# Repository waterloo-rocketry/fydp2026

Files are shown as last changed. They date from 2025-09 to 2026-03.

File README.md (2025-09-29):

# FYDP 2026 Electrical & Software

Sisyphus is a regeneratively cooled, 3D-printed liquid rocket engine. There are threee main electrical projects that support this system: Automedon, Achilles, and Theseus

## Automedon
Automedon is a repackaging of the team's existing EGSE stack (namely RLCS, DAQ, and GSPD) within two fully enclosed NEMA panels and with a redesigned power architecture. This vastly improves the robustness and utility of the system
Design doc: https://docs.google.com/document/d/1RASc9nuHLxcU_nNqpzqdATsLbMFS-u7HsDOORrnuTvM/edit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

## Achilles
Achilles, like its namesake, is designed to be an unkillable DAQ module that retains good analog performance. Unlike the team's previous COTS solutions, the system supports up to 30V common mode and differential signals, and is protected up to +/- 60V at the inputs.
DAQ v2 Design Doc (for context): https://docs.google.com/document/d/1antcjPh_7nqCMTjgXxEhXMyPKeuij0gU7g0J603f2qo/edit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

## Theseus
Theseus is the third iteration on the team's integrated propulsion avionics PCB. It is designed to read from pressure transducers, Hall sensors, and RTDs (which are very necessary for regen testing), as well as actuating solenoid valves

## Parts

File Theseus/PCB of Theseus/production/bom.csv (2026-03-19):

Designator | Footprint | Quantity | Value | LCSC Part #
3V3 | TestPoint_Pad_D2.0mm | 1 | TestPoint
C1, C2, C22 | 0603 | 3 | 10u
C10, C11 | 0603 | 2 | 2.2u
C12, C13, C15, C16, C17, C18, C19, C26, C3, C5, C9 | 0603 | 11 | 100n
C14 | 0603 | 1 | 1n
C20 | 0603 | 1 | 0.01uF
C21 | 0603 | 1 | 4.7u
C23, C24, C25, C4 | 0603 | 4 | 0.1u
C6, C7, C8 | 0603 | 3 | 22u
D1 | D_SOD-128 | 1 | PMEG3030EP
D2 | 1206 | 1 | WHITE
D3 | 1206 | 1 | BLUE
D4, D6 | 1206 | 2 | GREEN
D5, D7 | D_SOD-123 | 2 | CDBW140-G
F1 | FUSE_0154005.DR | 1 | 0154005.DRL
FB1 | 0603 | 1 | PE-0603PFB121ST
GND | TestPoint_Keystone_5000-5004_Miniature | 1 | TestPoint
J1 | connector_Harwin_G125-MH104M4-04AD000P | 1 | G125-MH104M4-04AD000P
J2 | 4DB-P108-02 | 1 | 4DB-P108-02
J3 | PinSocket_2x07_P1.27mm_Vertical_SMD | 1 | CN4 STDC14 (Programmer)
J4 | microSD_HC_Molex_47219-2001 | 1 | Micro SD Holder 0472192001
J5, J6, J7, J8 | connector_Harwin_G125–MG10605M4P | 4 | Conn_01x06_Socket
L1 | IND_SPM6530T-2R2M | 1 | SPM6530T-2R2M
Q1, Q2 | SOT_12UW-7_DIO | 2 | DMG1012UW-7
R1 | 0603 | 1 | 33.2k
R10, R11, R7, R8, R9 | 0603 | 5 | 51k
R12, R13, R14 | 0603 | 3 | 150R ±0.1%
R15, R17, R19 | 0603 | 3 | 82K
R16, R18, R20 | 0603 | 3 | 130K
R2 | 0603 | 1 | 10k
R21, R22 | 0603 | 2 | 150k
R23, R24 | 0603 | 2 | 100R
R25, R26 | 0603 | 2 | 649R
R27 | 0603 | 1 | 120R
R3 | 0603 | 1 | 300K
R4 | 0603 | 1 | 100K
R5, R6 | 0603 | 2 | 169R
TC+ | TestPoint_Pad_D2.0mm | 1 | TC1+
U1 | SOT-23-6_Handsoldering | 1 | TPS565201DDC
U2 | SOIC-8_3.9x4.9mm_P1.27mm | 1 | TCAN334
U3 | LQFP-100_14x14mm_P0.5mm | 1 | STM32H750VBTx
U4 | SOIC-8_5.3x5.3mm_P1.27mm | 1 | MX25L25645G
U5 | SOIC-8_3.9x4.9mm_P1.27mm | 1 | MAX6675
Y1 | Oscillator_SMD_Abracon_ASE-4Pin_3.2x2.5mm | 1 | ASE-4.000MHz-L-C-T

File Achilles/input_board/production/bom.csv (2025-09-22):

Designator | Footprint | Quantity | Value | LCSC Part #
C1, C59, C60 | 0805 | 3 | 10uF
C10, C12, C17, C19, C21, C23, C34, C37, C38, C6, C65, C68, C69 | 0805 | 13 | 1uF
C11, C58, C61, C8 | 0805 | 4 | 100nF
C13, C4 | 0805 | 2 | 10nF
C14 | 0805 | 1 | 300pF
C15 | 0805 | 1 | 6.8nF
C16, C18, C20, C22, C24, C25, C26, C27, C28, C29, C30, C31, C32, C33, C36, C70, C71 | 0805 | 17 | 0.1uF
C35 | 0805 | 1 | 0.33uF
C39 | 0805 | 1 | 2.2uF
C40, C43, C44, C45, C46, C47, C48, C49, C50, C51, C52, C53, C54 | 0805 | 13 | 100n
C41 | 0805 | 1 | 1u
C42 | 0805 | 1 | 4.7u
C5, C7 | 0805 | 2 | 4.7uF
C55 | 0805 | 1 | 10u
C56, C57 | 0805 | 2 | 2.2u
C62, C63, C64 | 0805 | 3 | 22uF
C66, C9 | 0805 | 2 | 1.6nF
C67 | 0805 | 1 | C
D1 | 1206 | 1 | BLUE
D2 | 1206 | 1 | GREEN
D3 | 1206 | 1 | RED
D4 | 1206 | 1 | WHITE
D5 | D_SMC_Handsoldering | 1 | SMCJ36CA
D6 | CR_SOD123F_DIO | 1 | B260S1F-7
F1 | 01530009Z | 1 | 5A
IC1 | QFN50P300X300X80-17N-D | 1 | LM5157RTER
IC10 | SOP50P490X110-10N | 1 | ADS8860IDGSR
IC2, IC3, IC4, IC5 | SOP65P640X120-20N | 4 | TMUX7349FPWR
IC6, IC7 | SOP65P640X120-16N | 2 | MUX509IPW
IC8 | SOP65P640X120-28N | 1 | MUX36D08IPW
IC9 | SOP65P640X120-16N | 1 | MUX508IPW
J1 | TerminalBlock_Phoenix_MKDS-1,5-2-5.08_1x02_P5.08mm_Horizontal | 1 | Screw_Terminal_01x02
J10 | PinSocket_2x02_P1.27mm_Vertical_SMD | 1 | Programmer
J11, J7 | TerminalBlock_Phoenix_MPT-0,5-2-2.54_1x02_P2.54mm_Horizontal | 2 | Screw_Terminal_01x02
J2 | PinHeader_1x03_P2.54mm_Vertical | 1 | Screw_Terminal_01x03
J3, J4, J5, J6 | TerminalBlock_Phoenix_MPT-0,5-8-2.54_1x08_P2.54mm_Horizontal | 4 | Screw_Terminal_01x08
J8 | CUI_UJ2-BH-1-TH | 1 | USB_B
J9 | PinHeader_1x03_P2.54mm_Vertical | 1 | CAN
L1 | IND_BOURNS_SRR5018 | 1 | SRR5018-3R9Y
L2 | IND_SRP1265A-2R2M | 1 | SRP1265A-2R2M
Q1 | VSON-8_3.3x3.3mm_P0.65mm_NexFET | 1 | CSD19537Q3
Q2 | SOT-23 | 1 | BSS138
R1 | 0805 | 1 | 510R
R10 | 0805 | 1 | 17kR
R11 | 0805 | 1 | 34kR
R12, R17, R18, R43, R47 | 0805 | 5 | 10kR
R13, R41 | 0805 | 2 | 20mR
R14 | 0805 | 1 | 203kR
R15 | 0805 | 1 | 1.29kR
R16 | 0805 | 1 | 75kR
R19, R4, R44 | 0805 | 3 | 500R
R2 | 0805 | 1 | 1.3kR
R20 | 0805 | 1 | 2.43kR
R21 | 0805 | 1 | 1.33k
R22 | 0805 | 1 | 9.76kR
R23, R24, R25, R26, R27, R28, R29, R30 | 0805 | 8 | 1kR
R3 | 0805 | 1 | 150R
R32 | 0805 | 1 | 6kR
R33 | 0805 | 1 | 1.2kR
R34 | 0805 | 1 | 667R
R35 | 0805 | 1 | 122R
R36 | 0805 | 1 | 60.6R
R37 | 0805 | 1 | 12R
R38 | 0805 | 1 | 6R
R39 | 0805 | 1 | 51kR
R40 | 0805 | 1 | 24kR
R42 | 0805 | 1 | 17.4kR
R45, R46 | 0805 | 2 | R_US
R5 | 0805 | 1 | 435kR
R6 | 0805 | 1 | 56kR
R7 | 0805 | 1 | 9.09kR
R8 | 0805 | 1 | 38.3kR
R9 | 0805 | 1 | 374kR
RN1, RN2 | SOT-23 | 2 | MAX5490TA05000-T
U1 | HTSSOP-20-1EP_4.4x6.5mm_P0.65mm_EP3.4x6.5mm_Mask2.96x2.96mm_ThermalVias | 1 | TPS26631PWP
U10, U11, U4, U5, U6, U7, U8, U9 | VSSOP-8_3x3mm_P0.65mm | 8 | INA849DGK
U12 | VSSOP-8_3x3mm_P0.65mm | 1 | REF6050xDGK
U13 | TO-263-3_TabPin2 | 1 | uA7805
U14 | SOT-23-5 | 1 | TPS76933
U15 | SOIC-8_3.9x4.9mm_P1.27mm | 1 | MCP2562
U16 | LQFP-144_20x20mm_P0.5mm | 1 | STM32H750ZBTx
U17 | SOT-23-6 | 1 | TPS565201
U18 | SOT-23-5_HandSoldering | 1 | INA180A3
U2 | Texas_RGW0020A_VQFN-20-1EP_5x5mm_P0.65mm_EP3.15x3.15mm_ThermalVias | 1 | TPS7A4701xRGW
U3 | SC70-5_DCK_TEX | 1 | INA290A3

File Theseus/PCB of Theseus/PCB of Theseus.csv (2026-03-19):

Reference | Qty | Value | DNP | Exclude from BOM | Exclude from Board | Footprint | Datasheet
C1,C2,C22 | 3 | 10u |  |  |  | Capacitor_SMD:C_0603_1608Metric_Pad1.08x0.95mm_HandSolder | ~
C3,C5,C9,C12,C13,C15,C16,C17,C18,C19,C26 | 11 | 100n |  |  |  | Capacitor_SMD:C_0603_1608Metric_Pad1.08x0.95mm_HandSolder | ~
C4,C23,C24,C25 | 4 | 0.1u |  |  |  | Capacitor_SMD:C_0603_1608Metric_Pad1.08x0.95mm_HandSolder | ~
C6,C7,C8 | 3 | 22u |  |  |  | Capacitor_SMD:C_0603_1608Metric_Pad1.08x0.95mm_HandSolder | ~
C10,C11 | 2 | 2.2u |  |  |  | Capacitor_SMD:C_0603_1608Metric_Pad1.08x0.95mm_HandSolder | ~
C14 | 1 | 1n |  |  |  | Capacitor_SMD:C_0603_1608Metric_Pad1.08x0.95mm_HandSolder | ~
C20 | 1 | 0.01uF |  |  |  | Capacitor_SMD:C_0603_1608Metric_Pad1.08x0.95mm_HandSolder | ~
C21 | 1 | 4.7u |  |  |  | Capacitor_SMD:C_0603_1608Metric_Pad1.08x0.95mm_HandSolder | ~
D1 | 1 | PMEG3030EP |  |  |  | Diode_SMD:D_SOD-128 | https://assets.nexperia.com/documents/data-sheet/PMEG3030EP.pdf
D2 | 1 | WHITE |  |  |  | LED_SMD:LED_1206_3216Metric_Pad1.42x1.75mm_HandSolder | ~
D3 | 1 | BLUE |  |  |  | LED_SMD:LED_1206_3216Metric_Pad1.42x1.75mm_HandSolder | ~
D4,D6 | 2 | GREEN |  |  |  | LED_SMD:LED_1206_3216Metric_Pad1.42x1.75mm_HandSolder | ~
D5,D7 | 2 | CDBW140-G |  |  |  | Diode_SMD:D_SOD-123 | https://www.mouser.ca/datasheet/3/819/1/CDBW120-G%20Thru.%20CDBW140-G%20RevE.pdf
F1 | 1 | 0154005.DRL |  |  |  | Fydp_footprints:FUSE_0154005.DR | ~
FB1 | 1 | PE-0603PFB121ST |  |  |  | Resistor_SMD:R_0603_1608Metric_Pad0.98x0.95mm_HandSolder | ~
H1,H2,H3,H4 | 4 | MountingHole |  | Excluded from BOM |  | MountingHole:MountingHole_3.2mm_M3_ISO14580 | ~
J1 | 1 | G125-MH104M4-04AD000P |  |  |  | canhw_footprints:connector_Harwin_G125-MH104M4-04AD000P | https://content.harwin.com/m/91a65d72bc24bdea/original/DRG-03150-Technical-Drawing-Datasheet-G125-MH1XXM4-XXAD000P-pdf.pdf
J2 | 1 | 4DB-P108-02 |  |  |  | canhw_footprints:4DB-P108-02 | ~
J3 | 1 | CN4 STDC14 (Programmer) |  |  |  | Connector_PinSocket_1.27mm:PinSocket_2x07_P1.27mm_Vertical_SMD | ~
J4 | 1 | Micro SD Holder 0472192001 |  |  |  | Connector_Card:microSD_HC_Molex_47219-2001 | https://www.we-online.com/components/products/datasheet/693072010801.pdf
J5,J6,J7,J8 | 4 | Conn_01x06_Socket |  |  |  | canhw_footprints:connector_Harwin_G125–MG10605M4P | ~
L1 | 1 | SPM6530T-2R2M |  |  |  | Fydp_footprints:IND_SPM6530T-2R2M | ~
Q1,Q2 | 2 | DMG1012UW-7 |  |  |  | Fydp_footprints:SOT_12UW-7_DIO | ~
R1 | 1 | 33.2k |  |  |  | Resistor_SMD:R_0603_1608Metric_Pad0.98x0.95mm_HandSolder | ~
R2 | 1 | 10k |  |  |  | Resistor_SMD:R_0603_1608Metric_Pad0.98x0.95mm_HandSolder | ~
R3 | 1 | 300K |  |  |  | Resistor_SMD:R_0603_1608Metric_Pad0.98x0.95mm_HandSolder | ~
R4 | 1 | 100K |  |  |  | Resistor_SMD:R_0603_1608Metric_Pad0.98x0.95mm_HandSolder | ~
R5,R6 | 2 | 169R |  |  |  | Resistor_SMD:R_0603_1608Metric_Pad0.98x0.95mm_HandSolder | ~
R7,R8,R9,R10,R11 | 5 | 51k |  |  |  | Resistor_SMD:R_0603_1608Metric_Pad0.98x0.95mm_HandSolder | ~
R12,R13,R14 | 3 | 150R ±0.1% |  |  |  | Resistor_SMD:R_0603_1608Metric_Pad0.98x0.95mm_HandSolder | ~
R15,R17,R19 | 3 | 82K |  |  |  | Resistor_SMD:R_0603_1608Metric_Pad0.98x0.95mm_HandSolder | ~
R16,R18,R20 | 3 | 130K |  |  |  | Resistor_SMD:R_0603_1608Metric_Pad0.98x0.95mm_HandSolder | ~
R21,R22 | 2 | 150k |  |  |  | Resistor_SMD:R_0603_1608Metric_Pad0.98x0.95mm_HandSolder | ~
R23,R24 | 2 | 100R |  |  |  | Resistor_SMD:R_0603_1608Metric_Pad0.98x0.95mm_HandSolder | ~
R25,R26 | 2 | 649R |  |  |  | Resistor_SMD:R_0603_1608Metric_Pad0.98x0.95mm_HandSolder | ~
R27 | 1 | 120R | DNP |  |  | Resistor_SMD:R_0603_1608Metric_Pad0.98x0.95mm_HandSolder | ~
TP1 | 1 | TestPoint |  |  |  | TestPoint:TestPoint_Pad_D2.0mm | ~
TP2 | 1 | TestPoint |  |  |  | TestPoint:TestPoint_Keystone_5000-5004_Miniature | ~
TP3 | 1 | TC1+ |  |  |  | TestPoint:TestPoint_Pad_D2.0mm | ~
U1 | 1 | TPS565201DDC |  |  |  | Package_TO_SOT_SMD:SOT-23-6_Handsoldering | https://www.ti.com/lit/ds/symlink/tps565201.pdf
U2 | 1 | TCAN334 |  |  |  | Package_SO:SOIC-8_3.9x4.9mm_P1.27mm | http://www.ti.com/lit/ds/symlink/tcan337.pdf
U3 | 1 | STM32H750VBTx |  |  |  | Package_QFP:LQFP-100_14x14mm_P0.5mm | https://www.st.com/resource/en/datasheet/stm32h750vb.pdf
U4 | 1 | MX25L25645G |  |  |  | Package_SO:SOIC-8_5.3x5.3mm_P1.27mm | https://www.mxic.com.tw/Lists/Datasheet/Attachments/8906/MX25L25645G,%203V,%20256Mb,%20v2.0.pdf
U5 | 1 | MAX6675 |  |  |  | Package_SO:SOIC-8_3.9x4.9mm_P1.27mm | https://www.analog.com/media/en/technical-documentation/data-sheets/MAX6675.pdf
Y1 | 1 | ASE-4.000MHz-L-C-T |  |  |  | Oscillator:Oscillator_SMD_Abracon_ASE-4Pin_3.2x2.5mm | http://www.abracon.com/Oscillators/ASV.pdf

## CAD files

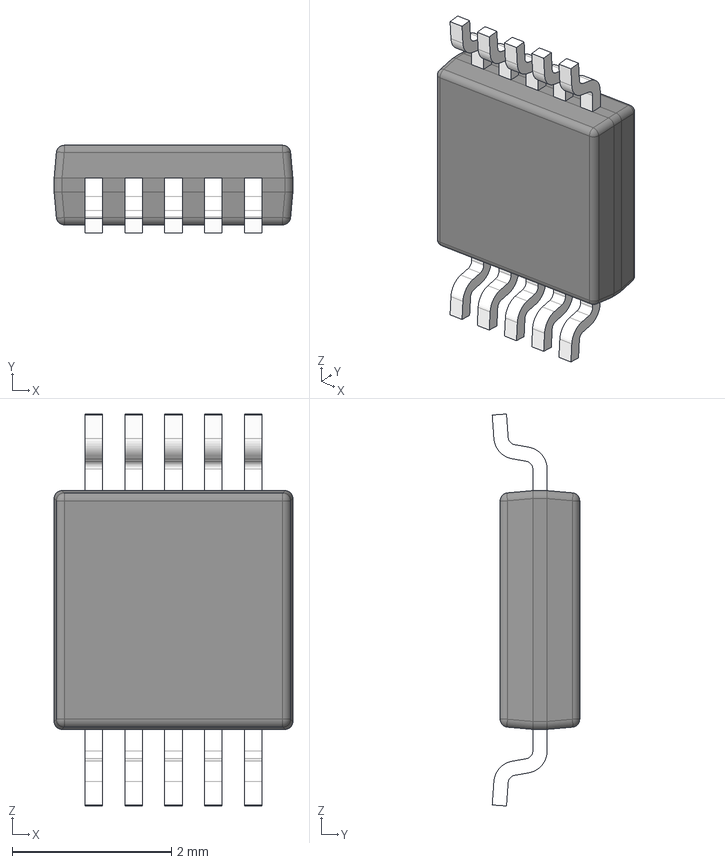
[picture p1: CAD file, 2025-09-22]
Achilles/input_board/3D/ADS8860IDGSR.stp
3.00 x 1.10 x 4.93 mm
BODY-SO
LEAD-SO x 10
PIN1-ID

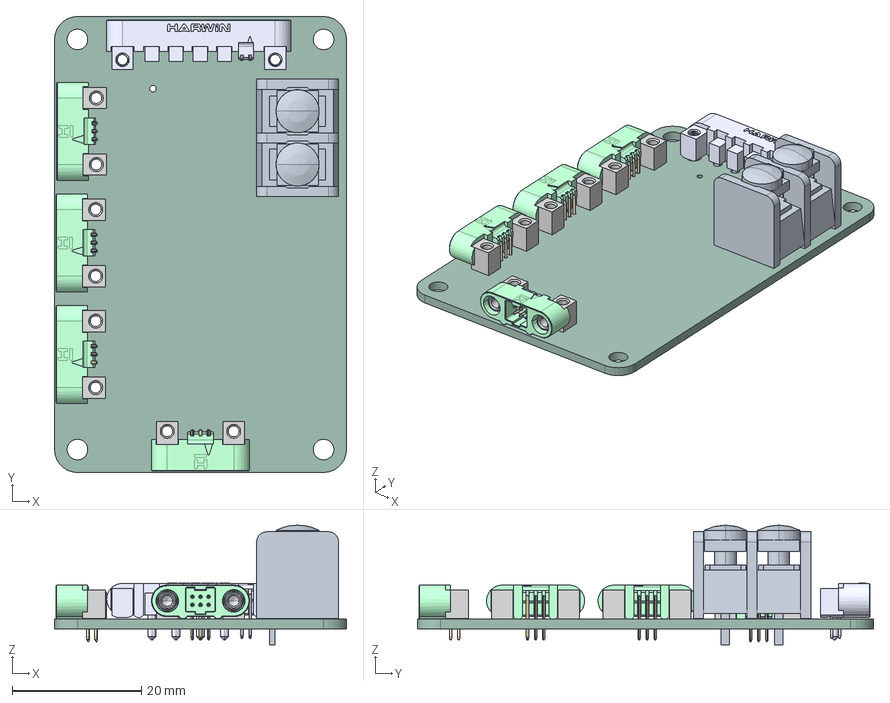
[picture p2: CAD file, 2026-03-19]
Theseus/PCB of Theseus/PCB of Theseus.step
45.2 x 70.6 x 18.5 mm
4DB-P108-02
G125-3270696 x 4
G125-1060005_BENT x 12
G125-1070005_BENT x 12
g125-mh104m4-04ad000p
PCB of Theseus_PCB

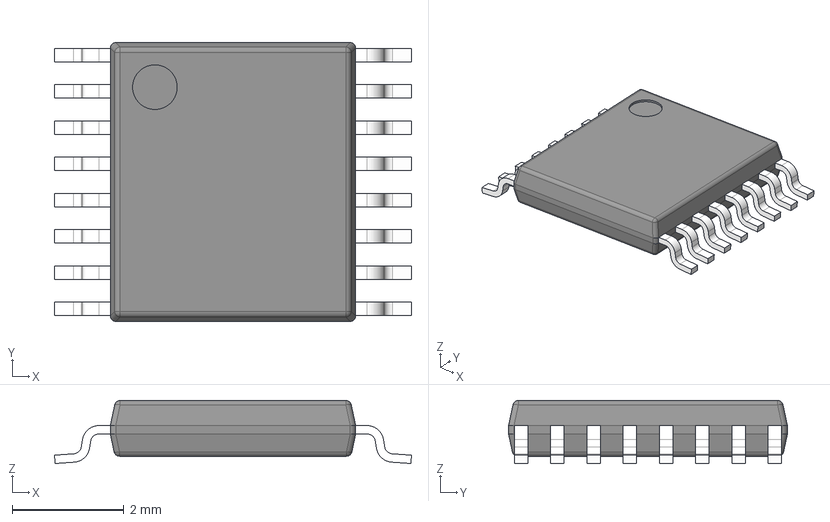
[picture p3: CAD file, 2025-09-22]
Achilles/input_board/3D/MUX509IPW.stp
6.40 x 5.00 x 1.13 mm
BODY-TSSOP
LEAD-TSSOP x 16
PIN1

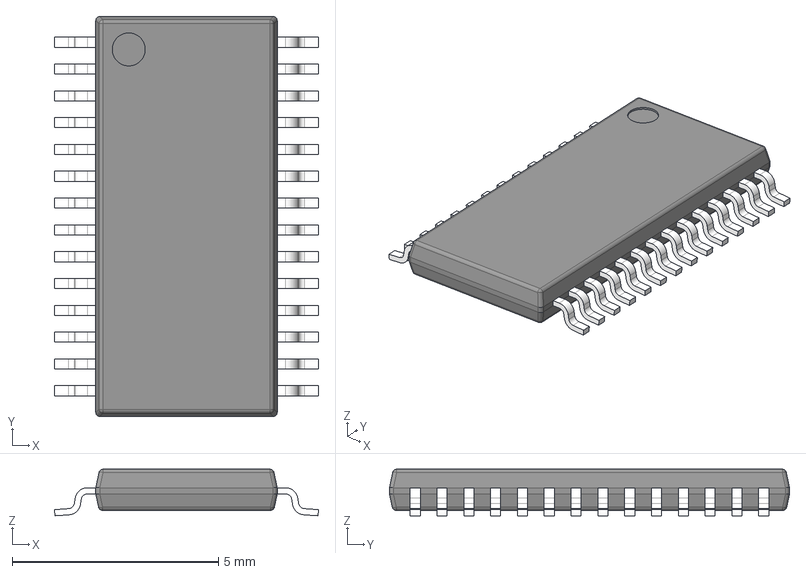
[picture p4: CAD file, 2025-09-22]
Achilles/input_board/3D/MUX36D08IPW.stp
6.40 x 9.70 x 1.13 mm
BODY-TSSOP
LEAD-TSSOP x 28
PIN1

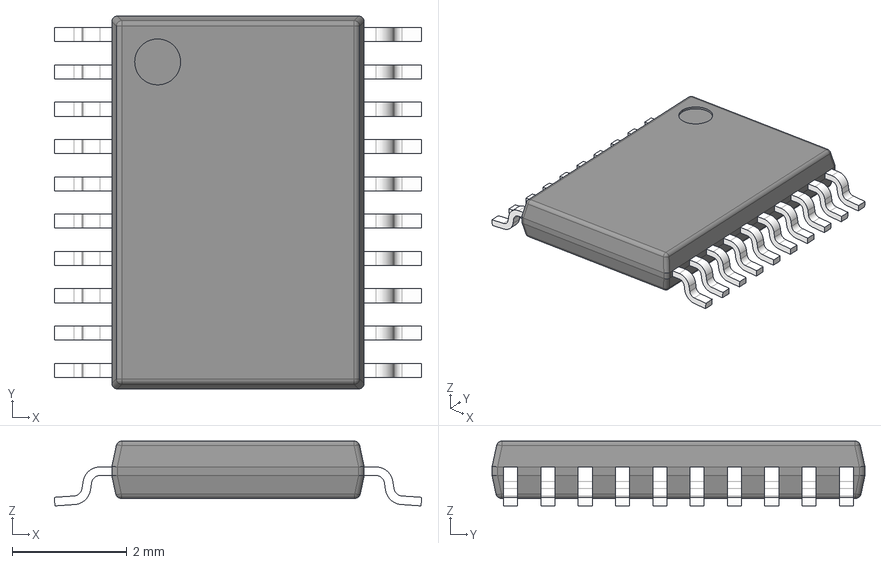
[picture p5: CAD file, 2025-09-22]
Achilles/input_board/3D/TMUX7348FPWR.stp
6.40 x 6.50 x 1.13 mm
BODY-TSSOP
LEAD-TSSOP x 20
PIN1

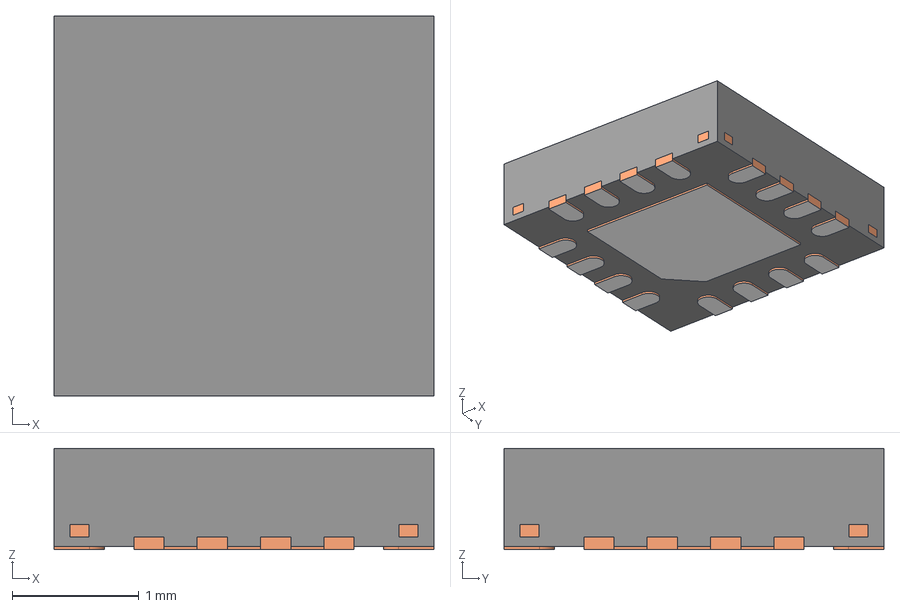
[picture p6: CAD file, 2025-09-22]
Achilles/input_board/3D/LM5157RTER.stp
3.00 x 3.00 x 0.8 mm
BODY-QFN
FRAME-RTE0016C
PIN1-ID

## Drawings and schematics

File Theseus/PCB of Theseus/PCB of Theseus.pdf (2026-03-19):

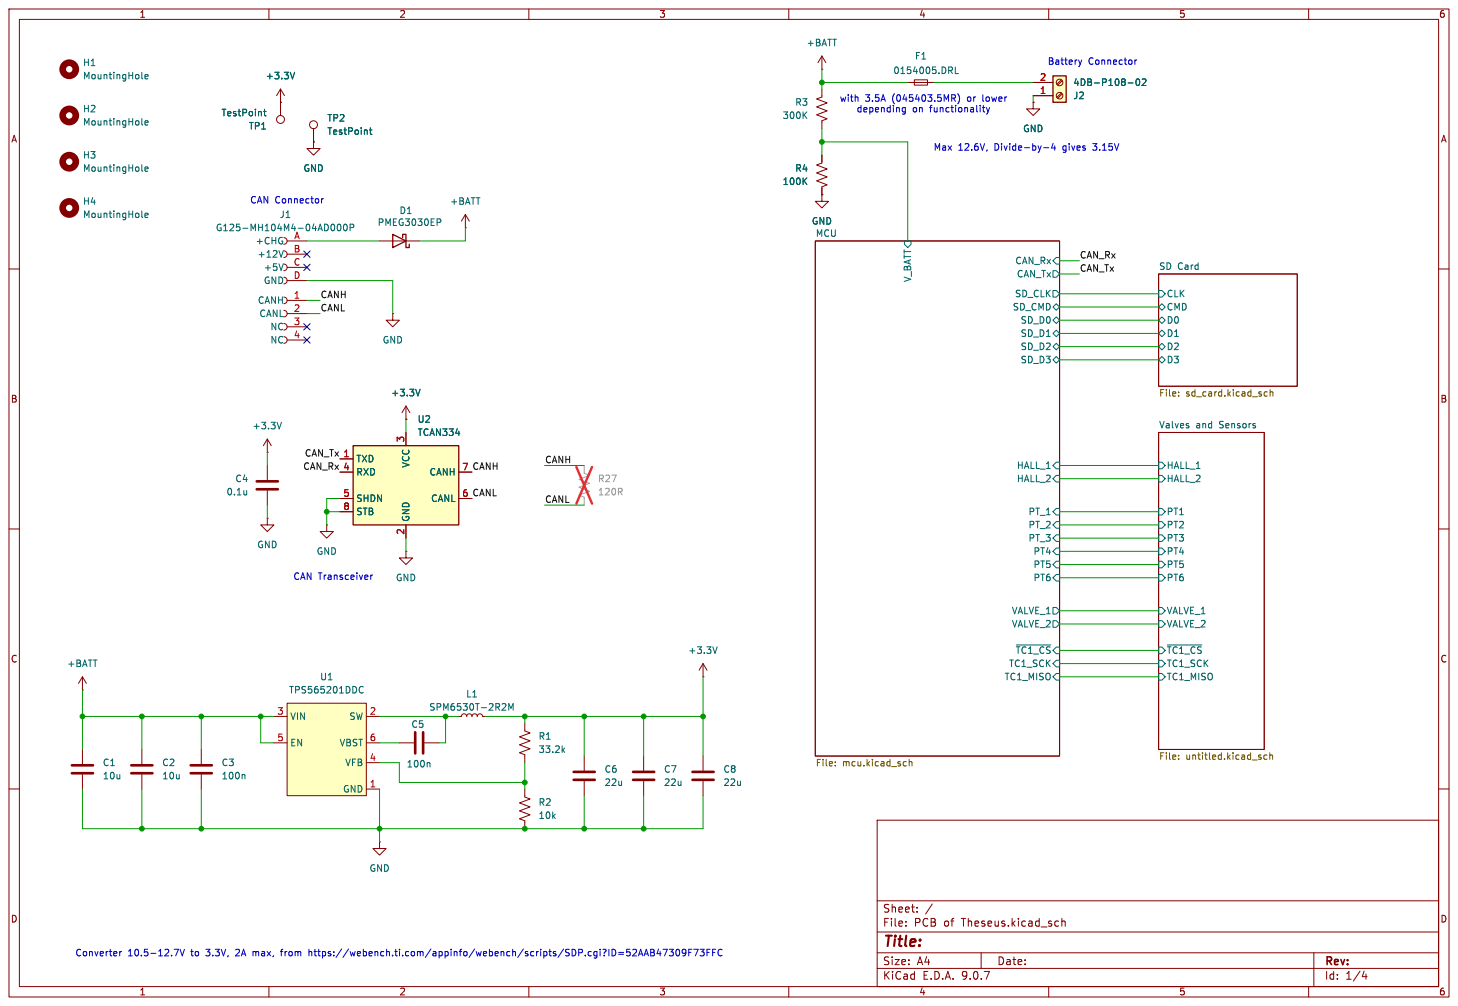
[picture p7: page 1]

CANH 1 CANL 2 NC 3 NC 4

CLK CMD
VALVE_2 Valves and Sensors File: untitled.kicad_sch

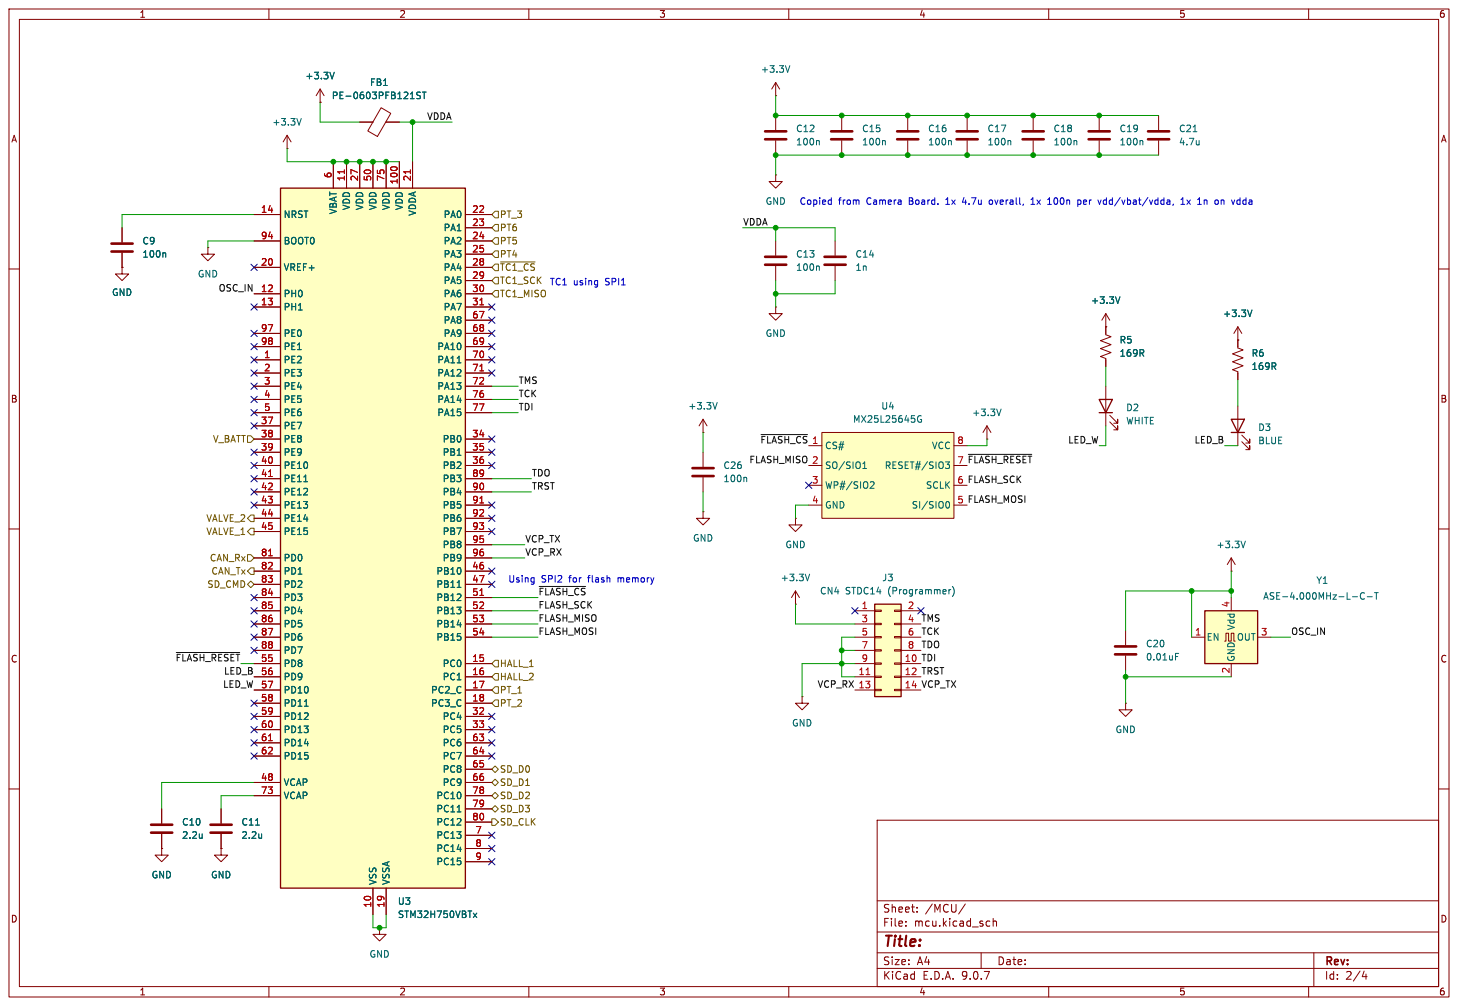
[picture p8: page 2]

6 VDD 11 VDD 27 VDD 50 VSS 10 VDD 75 VSSA 19 VDD 100 VDDA 21 PA0 22 PA1 23 PA2 24 PA3 25 PA4 28 PA5 29 PA6 30 PA7 31 PA8 67 PA9 68 PA10 69 PA11 70 PA12 71 PA13 72 PA14 76 PA15 77 PB0 34 PB1 35 PB2 36 PB3 89 PB4 90 PB5 91 PB6 92 PB7 93 PB8 95 PB9 96 PB10 46 PB11 47 PB12 51 PB13 52 PB14 53 PB15 54 PC0 15 PC1 16 PC2_C 17 PC3_C 18 PC4 32 PC5 33 PC6 63 PC7 64 PC8 65 PC9 66 PC10 78 PC11 79 PC12 80 PC13 7 PC14 8 PC15 9 C10

6 VDD 11 VDD 27 VDD 50 VSS 10 VDD 75 VSSA 19 VDD 100 VDDA 21 PA0 22 PA1 23 PA2 24 PA3 25 PA4 28 PA5 29 PA6 30 PA7 31 PA8 67 PA9 68 PA10 69 PA11 70 PA12 71 PA13 72 PA14 76 PA15 77 PB0 34 PB1 35 PB2 36 PB3 89 PB4 90 PB5 91 PB6 92 PB7 93 PB8 95 PB9 96 PB10 46 PB11 47 PB12 51 PB13 52 PB14 53 PB15 54 PC0 15 PC1 16 PC2_C 17 PC3_C 18 PC4 32 PC5 33 PC6 63 PC7 64 PC8 65 PC9 66 PC10 78 PC11 79 PC12 80 PC13 7 PC14 8 PC15 9 U3STM32H750VBTx

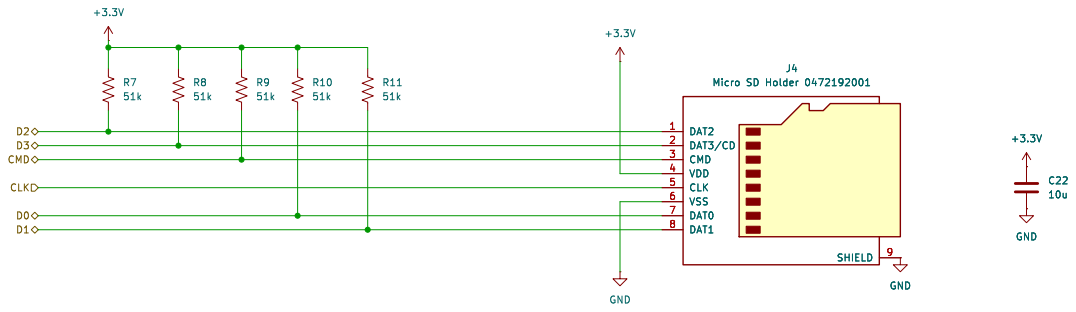
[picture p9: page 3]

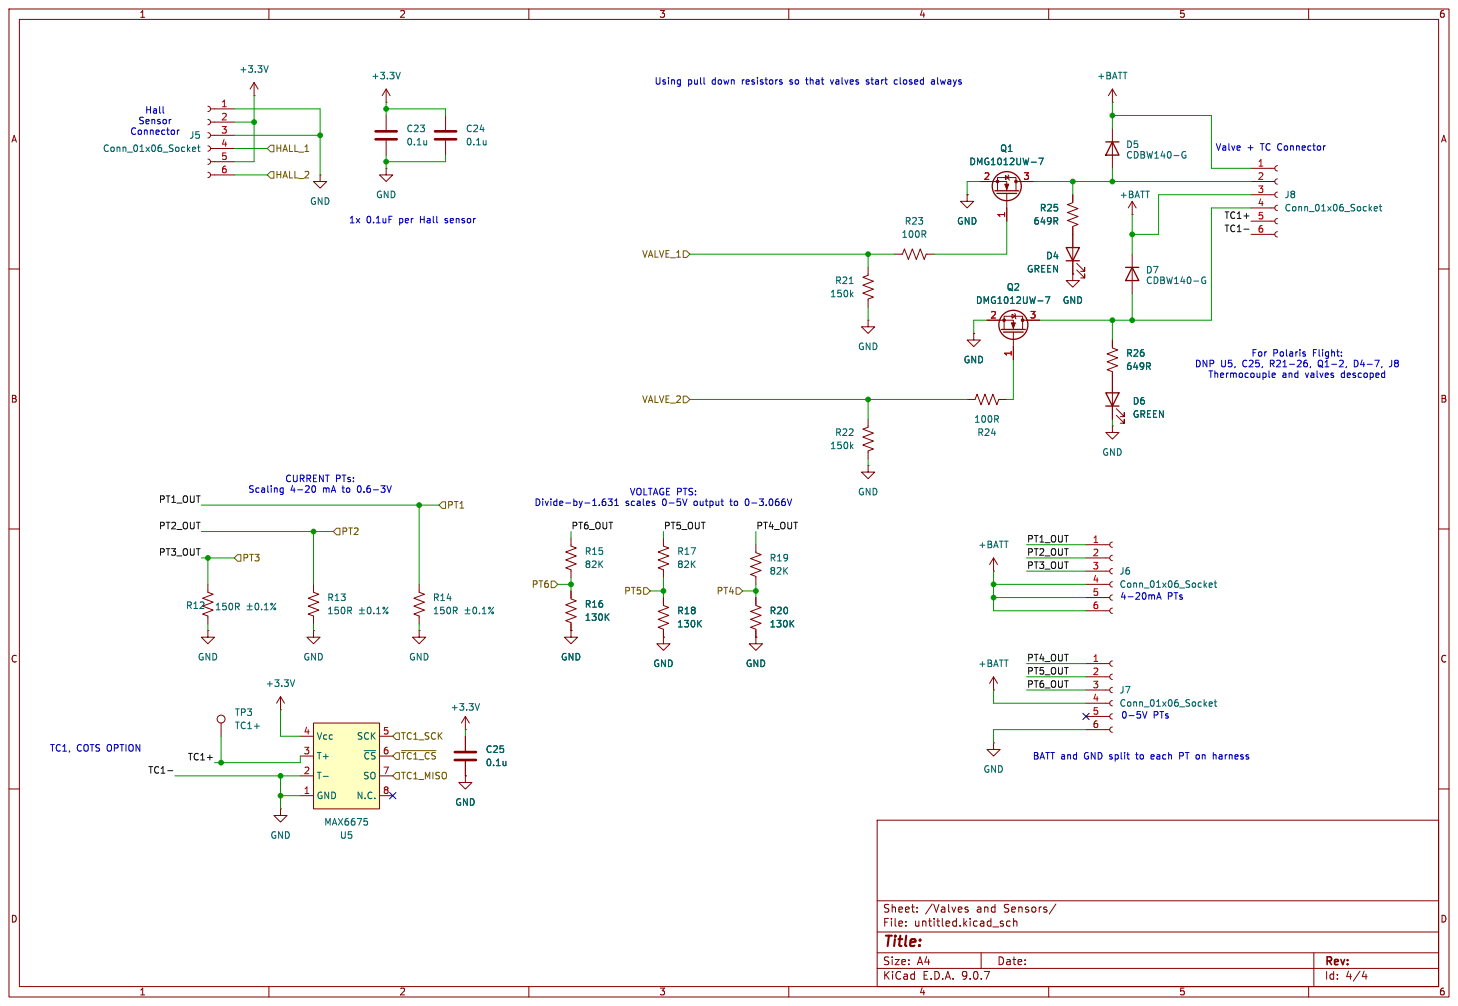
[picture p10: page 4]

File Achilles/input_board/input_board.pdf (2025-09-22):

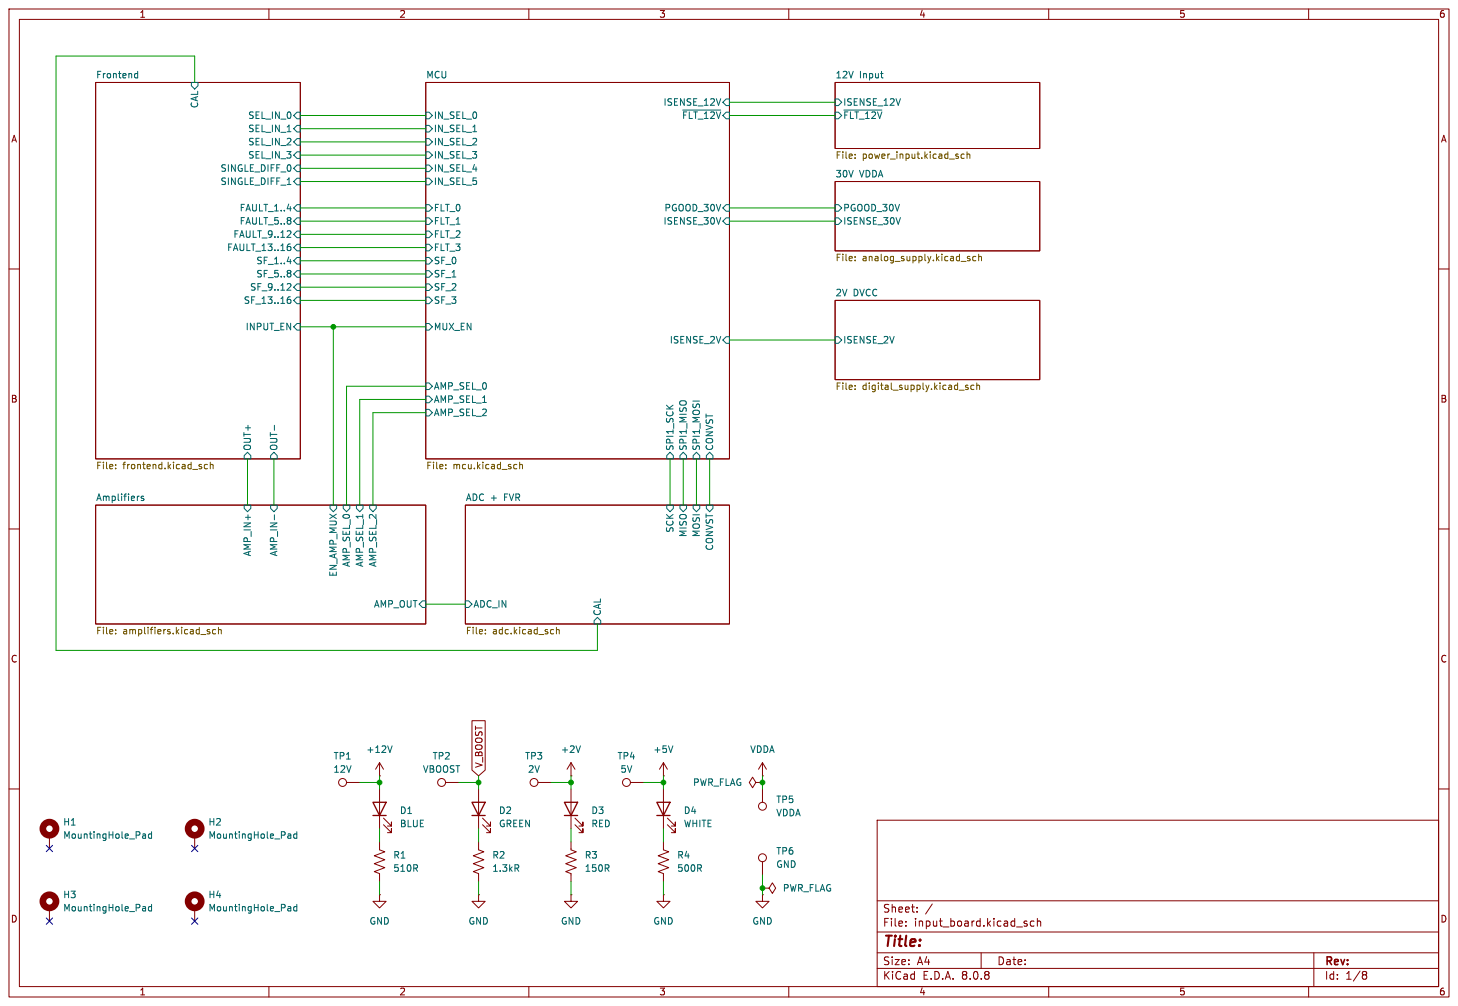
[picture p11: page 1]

Id: 1/8 Title: File: input_board.kicad_sch Sheet: /

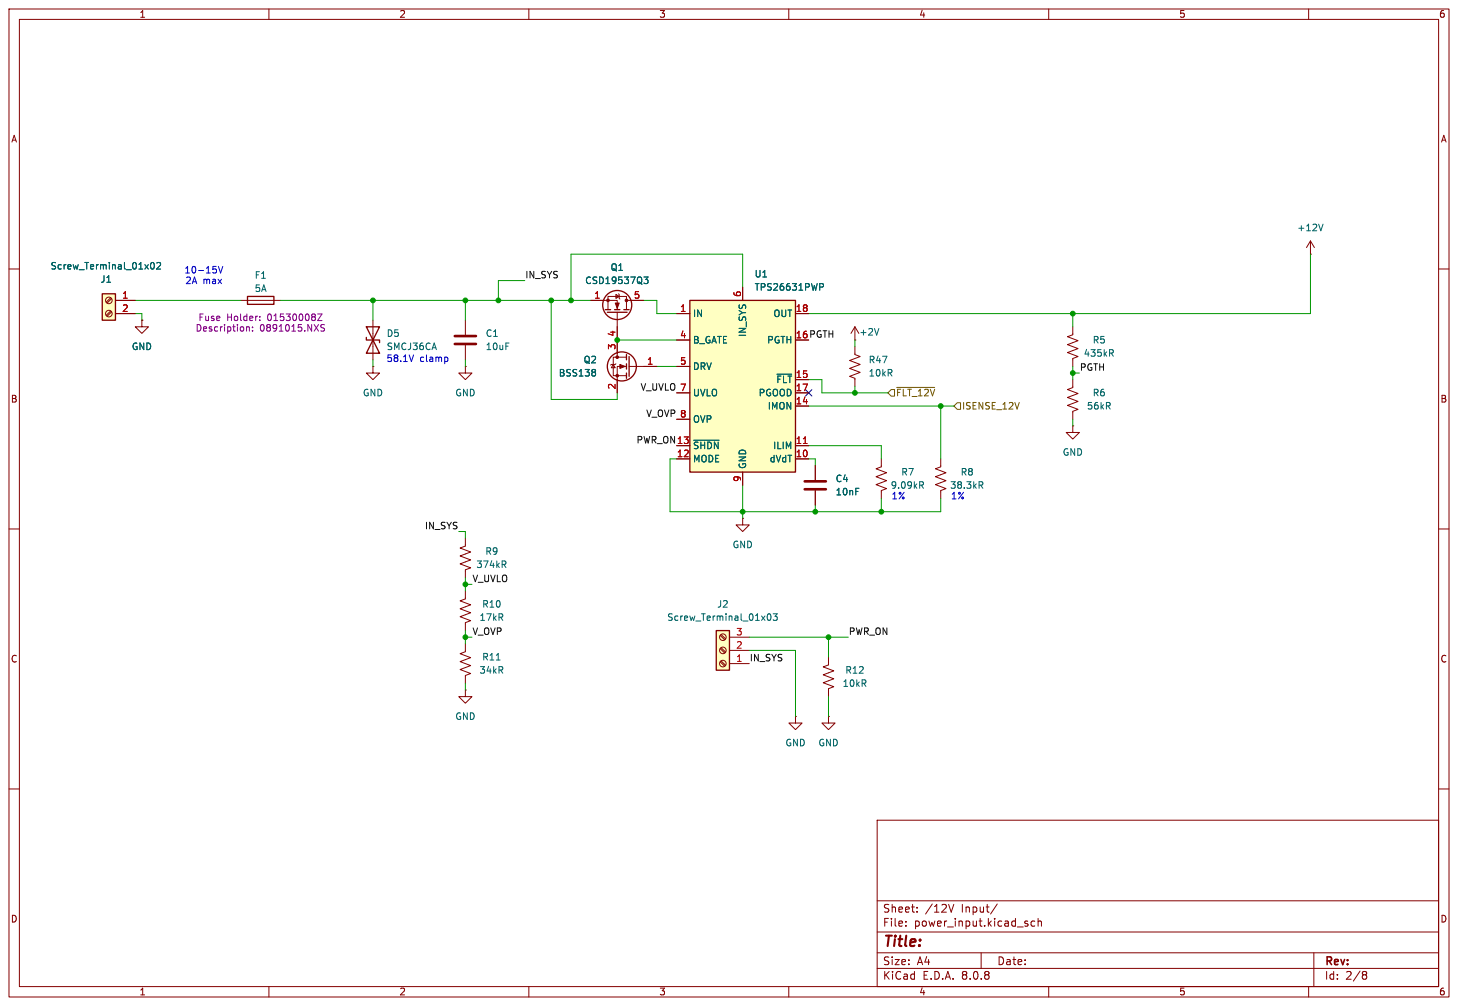
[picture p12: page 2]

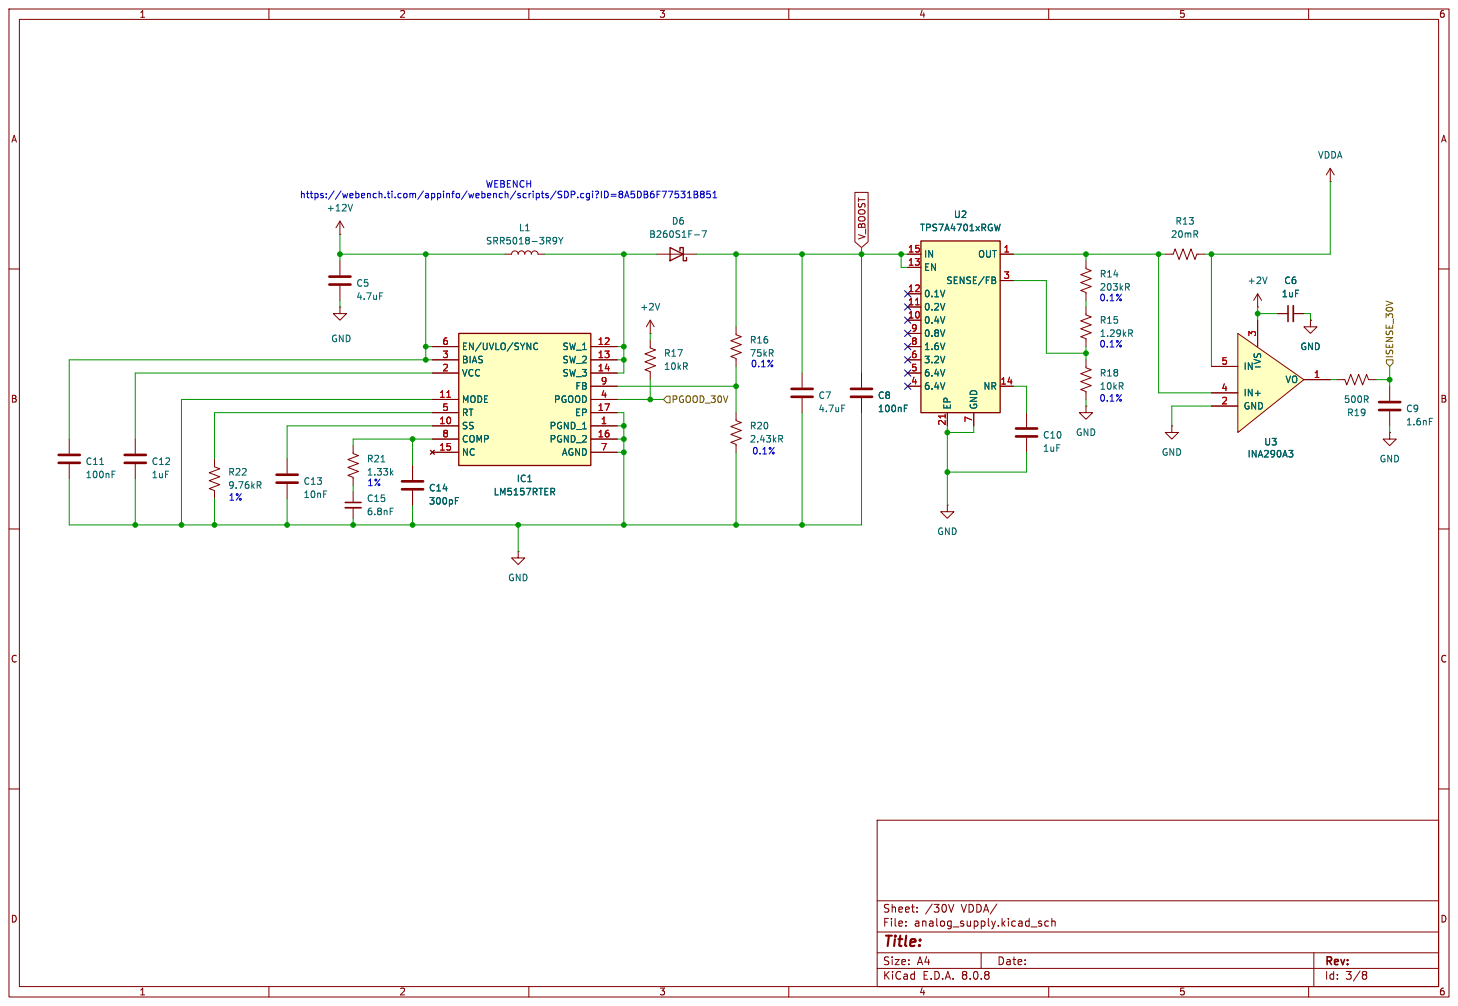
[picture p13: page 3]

https://webench.ti.com/appinfo/webench/scripts/SDP.cgi?ID=8A5DB6F77531B851

Id: 3/8 Title: File: analog_supply.kicad_sch Sheet: /30V VDDA/

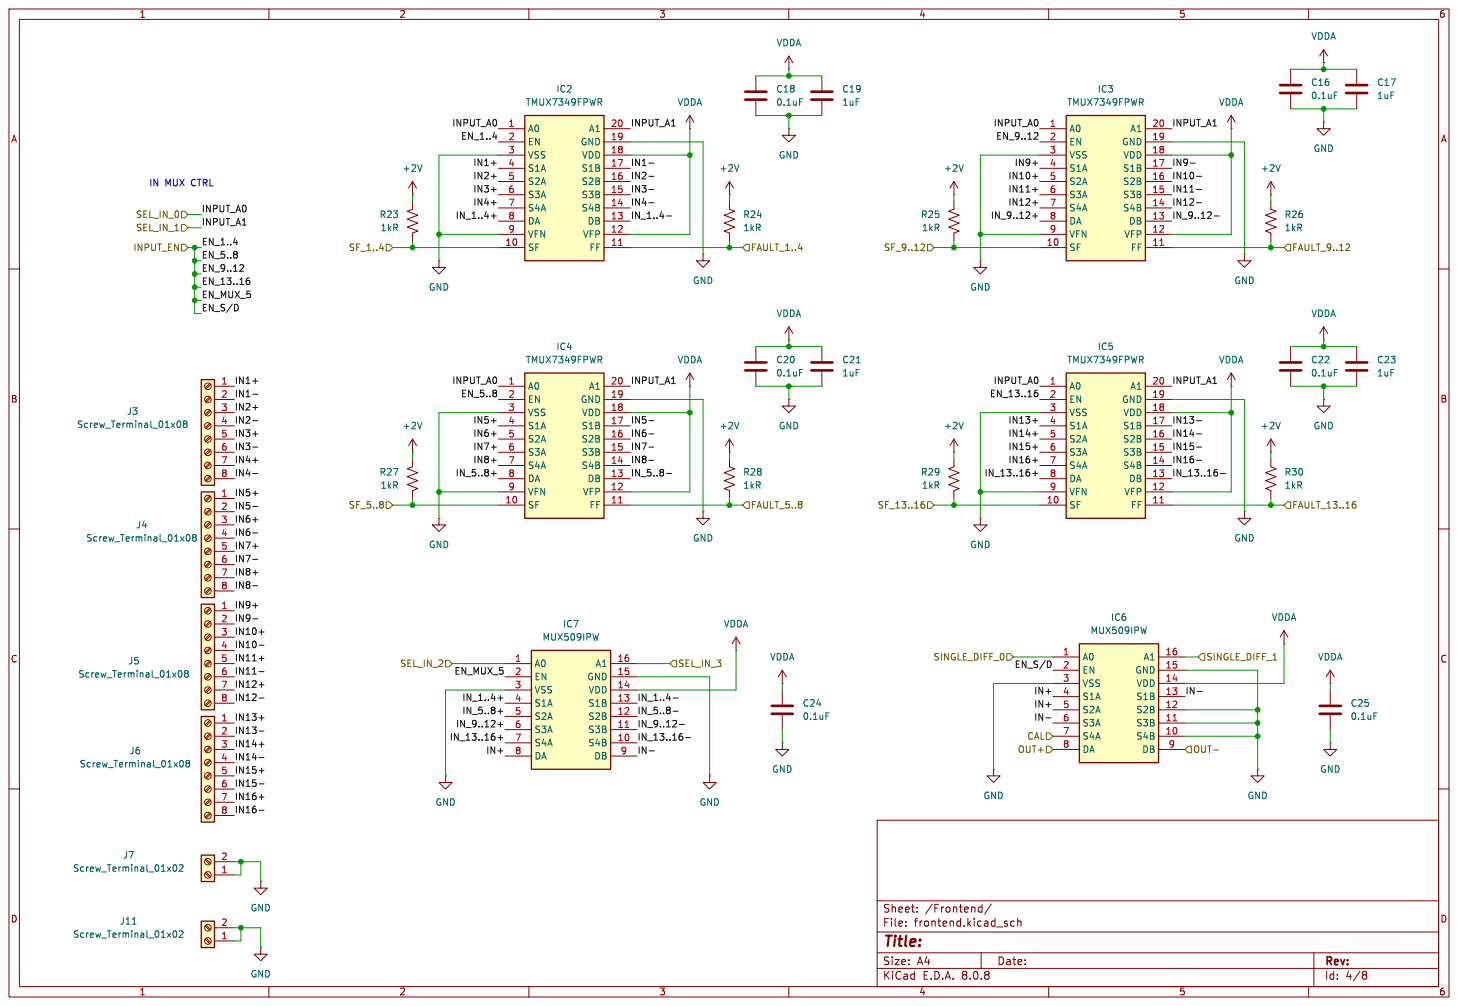
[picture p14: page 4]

Id: 4/8 Title: File: frontend.kicad_sch Sheet: /Frontend/ R29

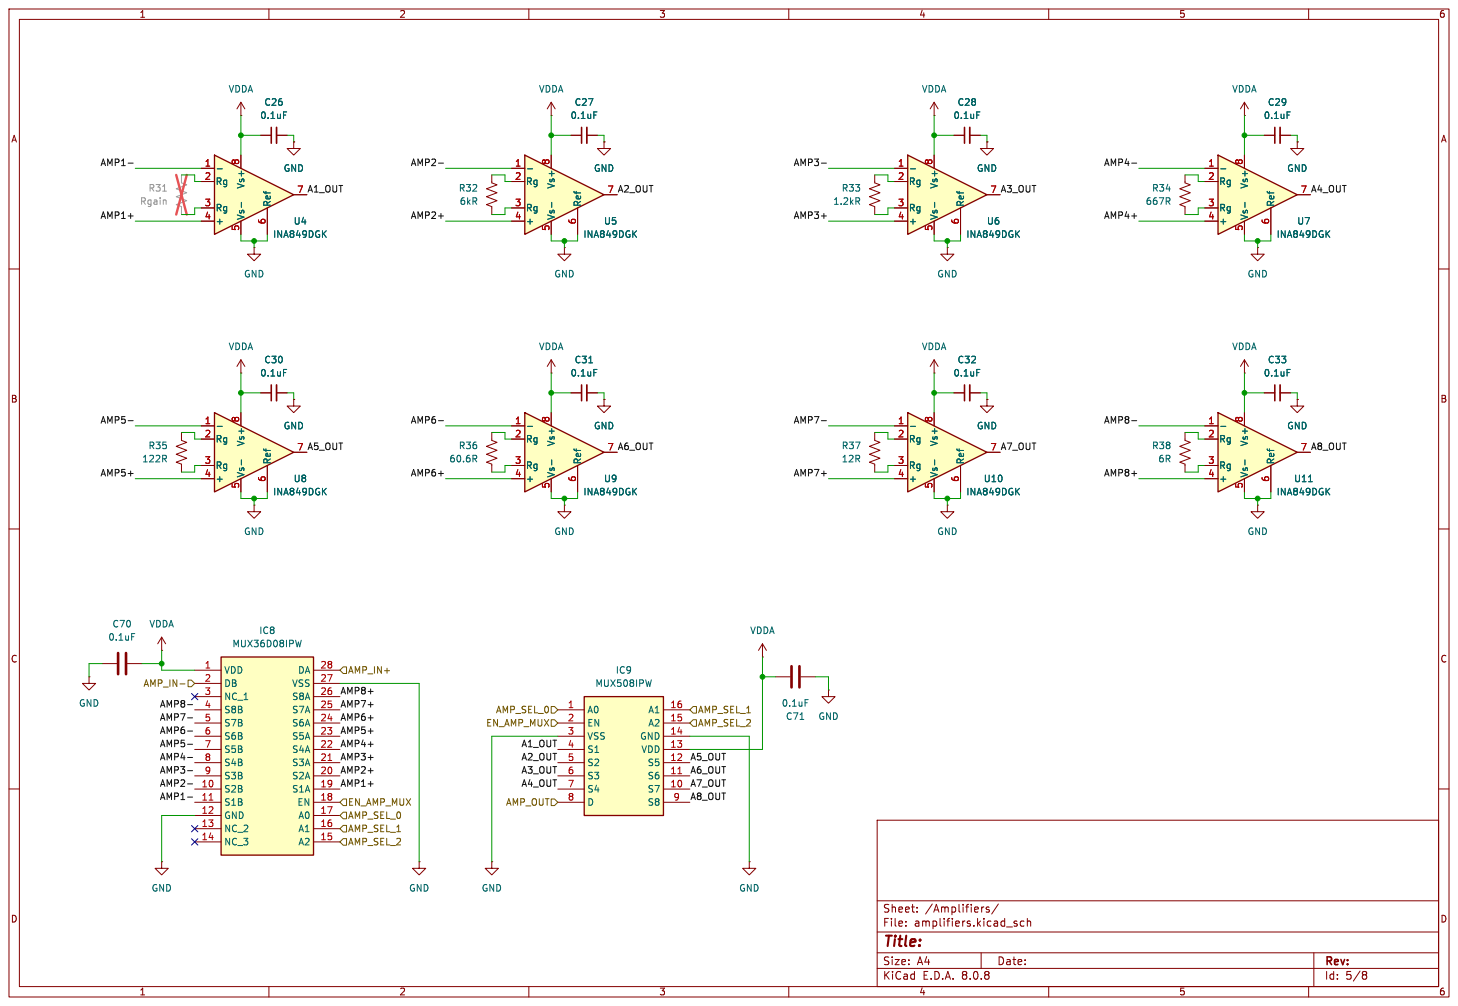
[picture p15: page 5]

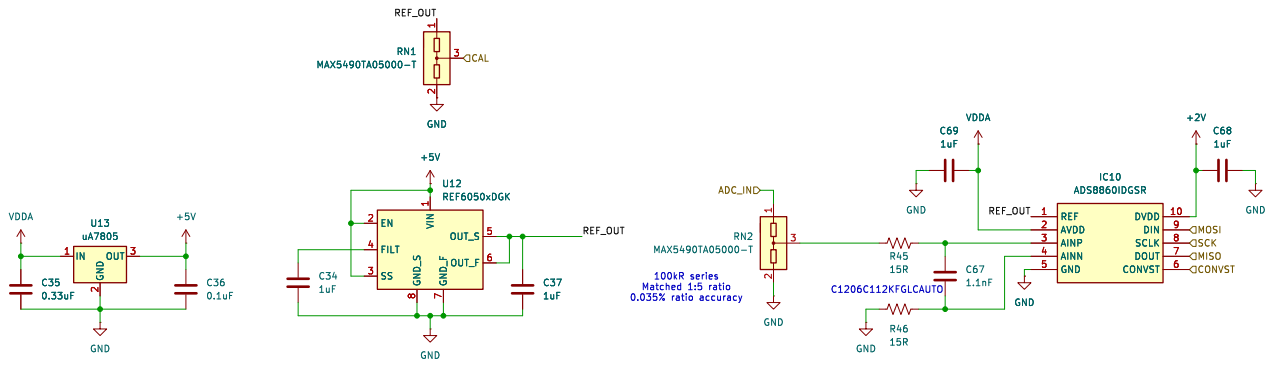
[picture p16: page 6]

1 2 RN1 3 MAX5490TA05000-T REF 1 DVDD 10 AVDD 2 AINP 3 AINN 4 GND 5 CONVST 6 DOUT 7 SCLK 8 DIN 9

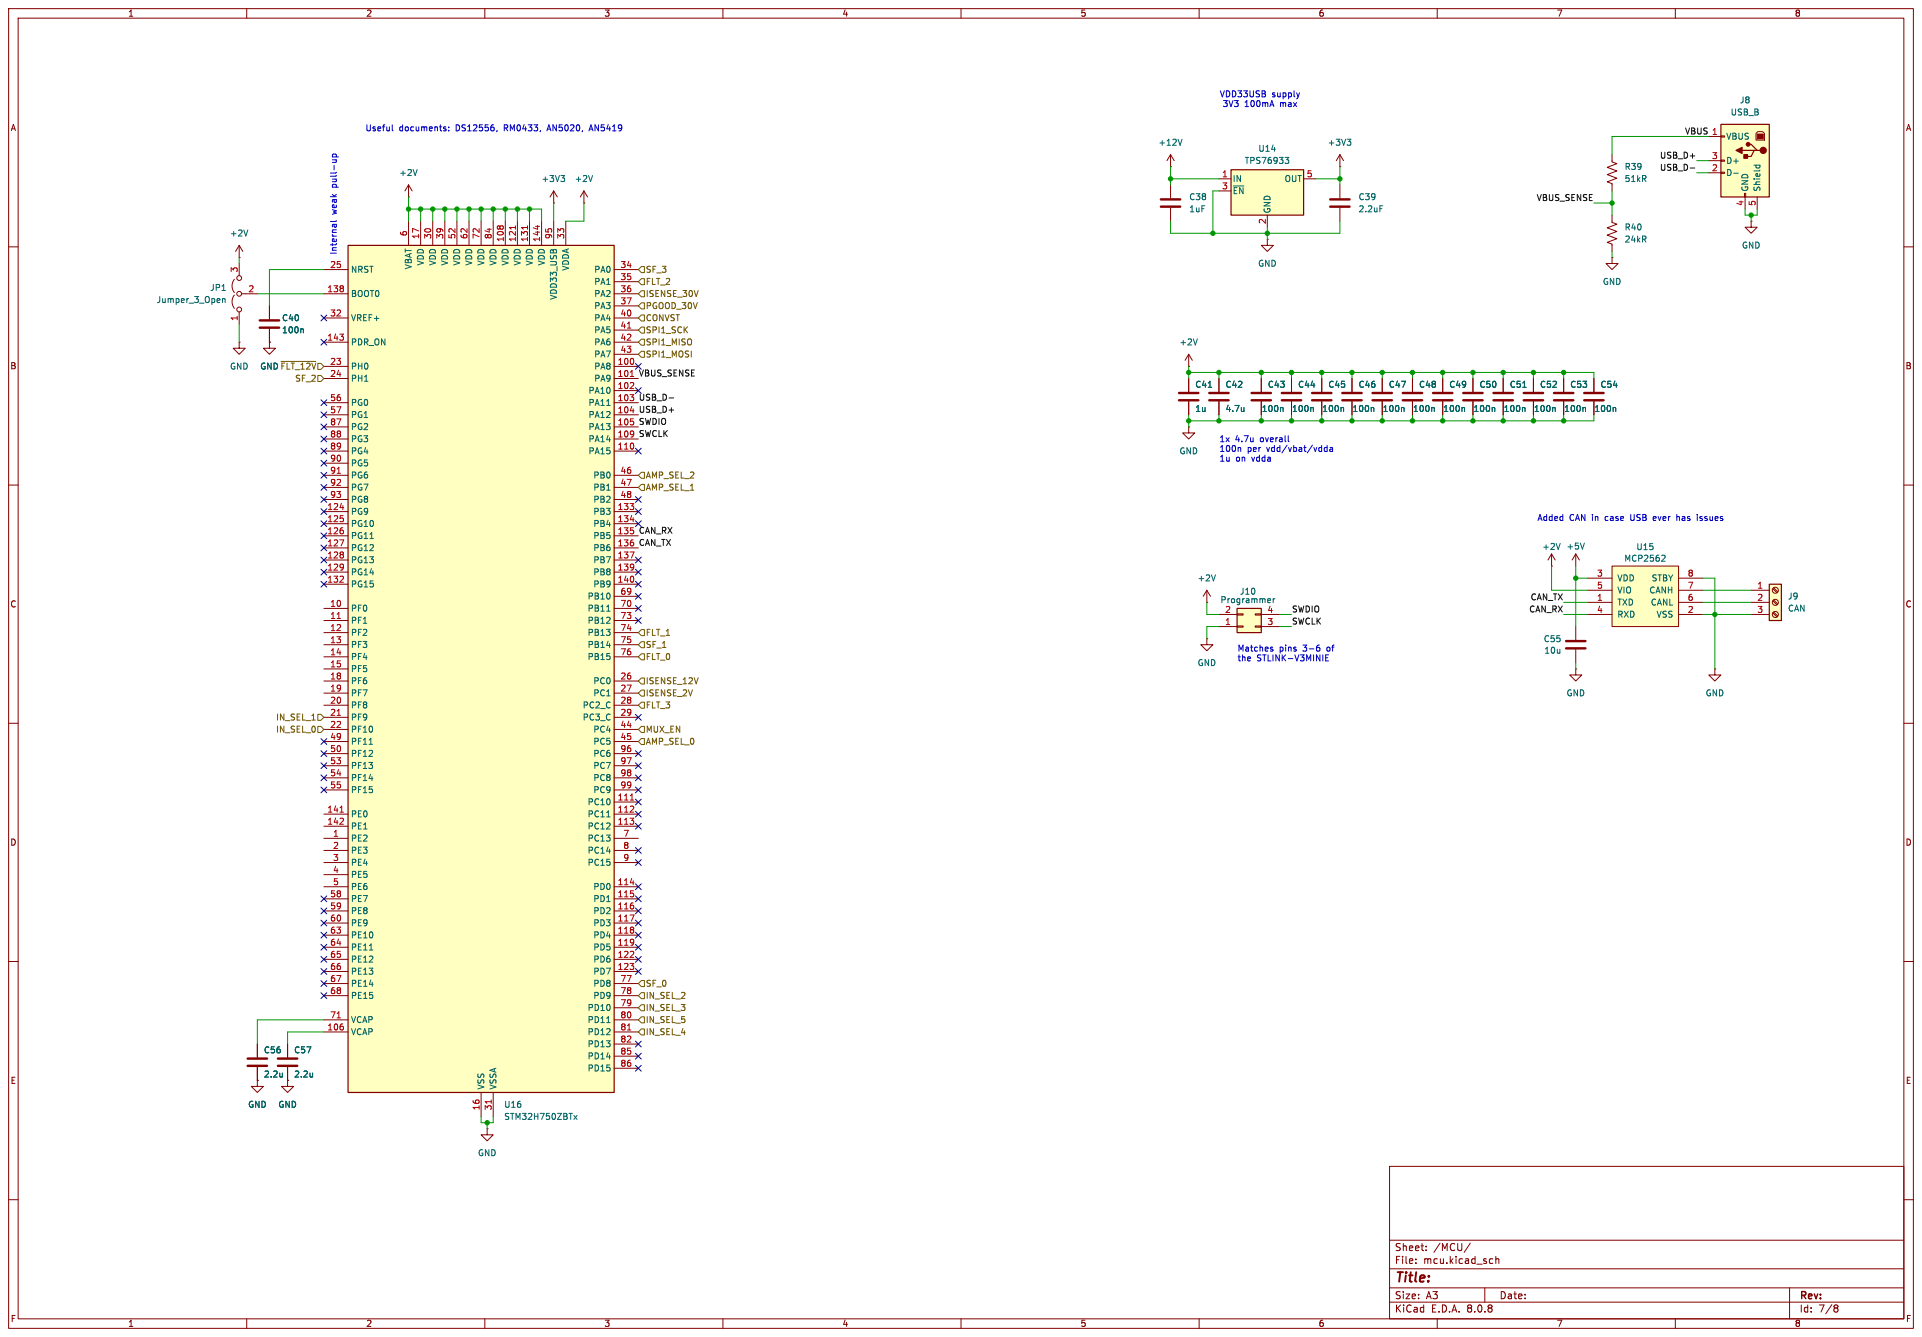
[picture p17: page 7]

Id: 7/8 Title: File: mcu.kicad_sch Sheet: /MCU/

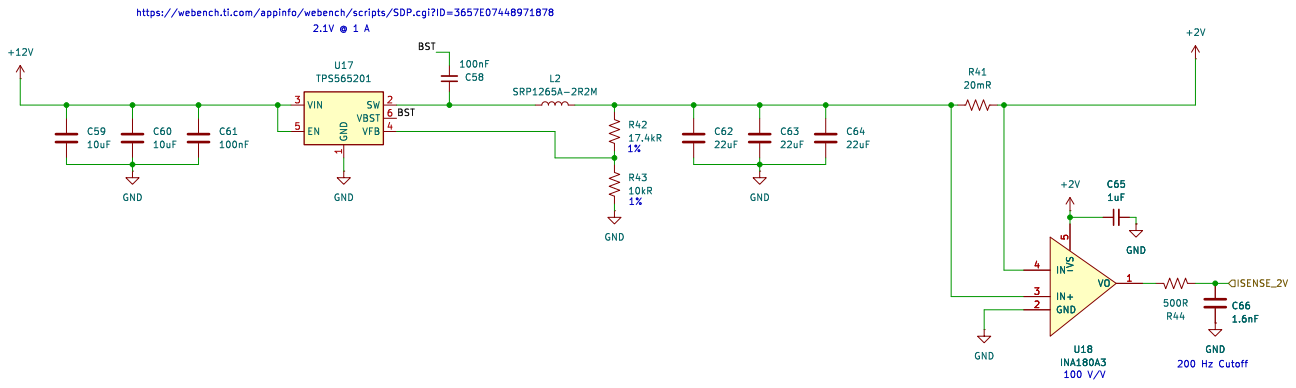
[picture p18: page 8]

200 Hz Cutoff https://webench.ti.com/appinfo/webench/scripts/SDP.cgi?ID=3657E07448971878

1 SW 2 VIN 3 VFB 4 EN 5 VBST 6 U17 TPS565201 C61

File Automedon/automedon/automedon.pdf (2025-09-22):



Id: 2/6 Title: File: power.kicad_sch Sheet: /power/


Id: 3/6 Title: File: tank_heating.kicad_sch Sheet: /tank_heating/



Id: 5/6 Title: File: ethernet.kicad_sch Sheet: /ethernet/ GND






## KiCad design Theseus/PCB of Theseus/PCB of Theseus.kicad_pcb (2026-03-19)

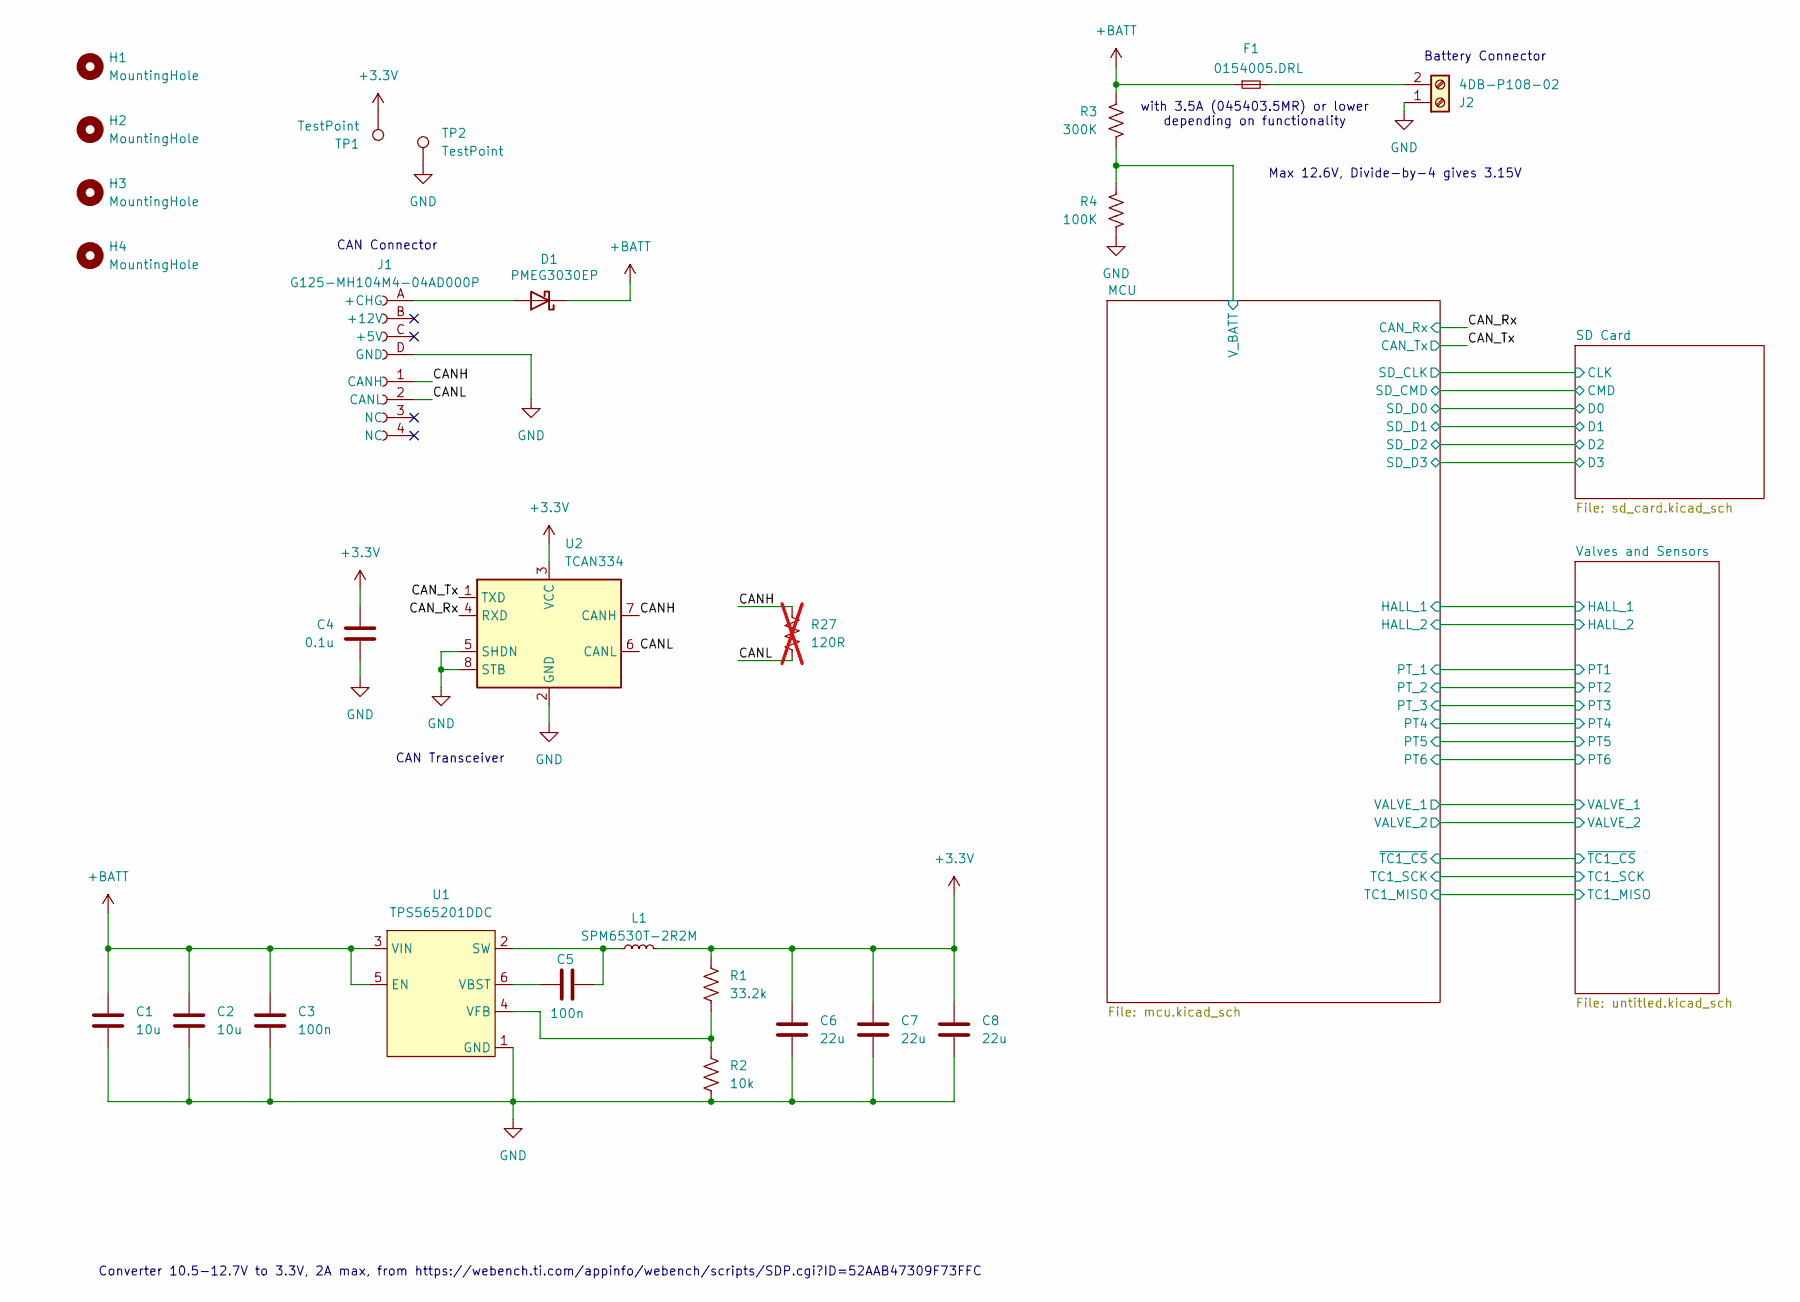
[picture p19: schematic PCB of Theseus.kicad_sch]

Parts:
C1, C2: 10u; C_0603_1608Metric_Pad1.08x0.95mm_HandSolder
C3, C5: 100n; C_0603_1608Metric_Pad1.08x0.95mm_HandSolder
C4: 0.1u; C_0603_1608Metric_Pad1.08x0.95mm_HandSolder
C6, C7, C8: 22u; C_0603_1608Metric_Pad1.08x0.95mm_HandSolder
D1: PMEG3030EP; D_SOD-128
F1: 0154005.DRL; FUSE_0154005.DR
H1, H2, H3, H4: MountingHole; MountingHole_3.2mm_M3_ISO14580
J1: G125-MH104M4-04AD000P; connector_Harwin_G125-MH104M4-04AD000P
J2: 4DB-P108-02
L1: SPM6530T-2R2M; IND_SPM6530T-2R2M
R1: 33.2k; R_0603_1608Metric_Pad0.98x0.95mm_HandSolder
R2: 10k; R_0603_1608Metric_Pad0.98x0.95mm_HandSolder
R3: 300K; R_0603_1608Metric_Pad0.98x0.95mm_HandSolder
R4: 100K; R_0603_1608Metric_Pad0.98x0.95mm_HandSolder
R27: 120R; R_0603_1608Metric_Pad0.98x0.95mm_HandSolder; not fitted
TP1: TestPoint; TestPoint_Pad_D2.0mm
TP2: TestPoint; TestPoint_Keystone_5000-5004_Miniature
U1: TPS565201DDC; SOT-23-6_Handsoldering
U2: TCAN334; SOIC-8_3.9x4.9mm_P1.27mm

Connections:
+3.3V: C4.1, C6.1, C7.1, C8.1, L1.1, R1.1, TP1.1, U2.3 (VCC); also elsewhere on the board
+BATT: C1.1, C2.1, C3.1, D1.1 (K), F1.1, R3.1, U1.3 (VIN), U1.5 (EN); also elsewhere on the board
/CANH: J1.1 (CANH), R27.1, U2.7 (CANH)
/CANL: J1.2 (CANL), R27.2, U2.6 (CANL)
/CAN_Rx: U2.4 (RXD); also elsewhere on the board
/CAN_Tx: U2.1 (TXD); also elsewhere on the board
/MCU/V_BATT: R3.2, R4.1; also elsewhere on the board
GND: C1.2, C2.2, C3.2, C4.2, C6.2, C7.2, C8.2, J1.D (GND), J2.1, R2.2, R4.2, TP2.1, U1.1 (GND), U2.2 (GND), U2.5 (SHDN), U2.8 (STB); also elsewhere on the board
unnamed: D1.2 (A), J1.A (+CHG)
unnamed: F1.2, J2.2
unnamed: C5.1, L1.2, U1.2 (SW)
unnamed: C5.2, U1.6 (VBST)
unnamed: R1.2, R2.1, U1.4 (VFB)

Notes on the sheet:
Converter 10.5-12.7V to 3.3V, 2A max, from https://webench.ti.com/appinfo/webench/scripts/SDP.cgi?ID=52AAB47309F73FFC
Max 12.6V, Divide-by-4 gives 3.15V
with 3.5A (045403.5MR) or lower depending on functionality
CAN Connector
Battery Connector
CAN Transceiver

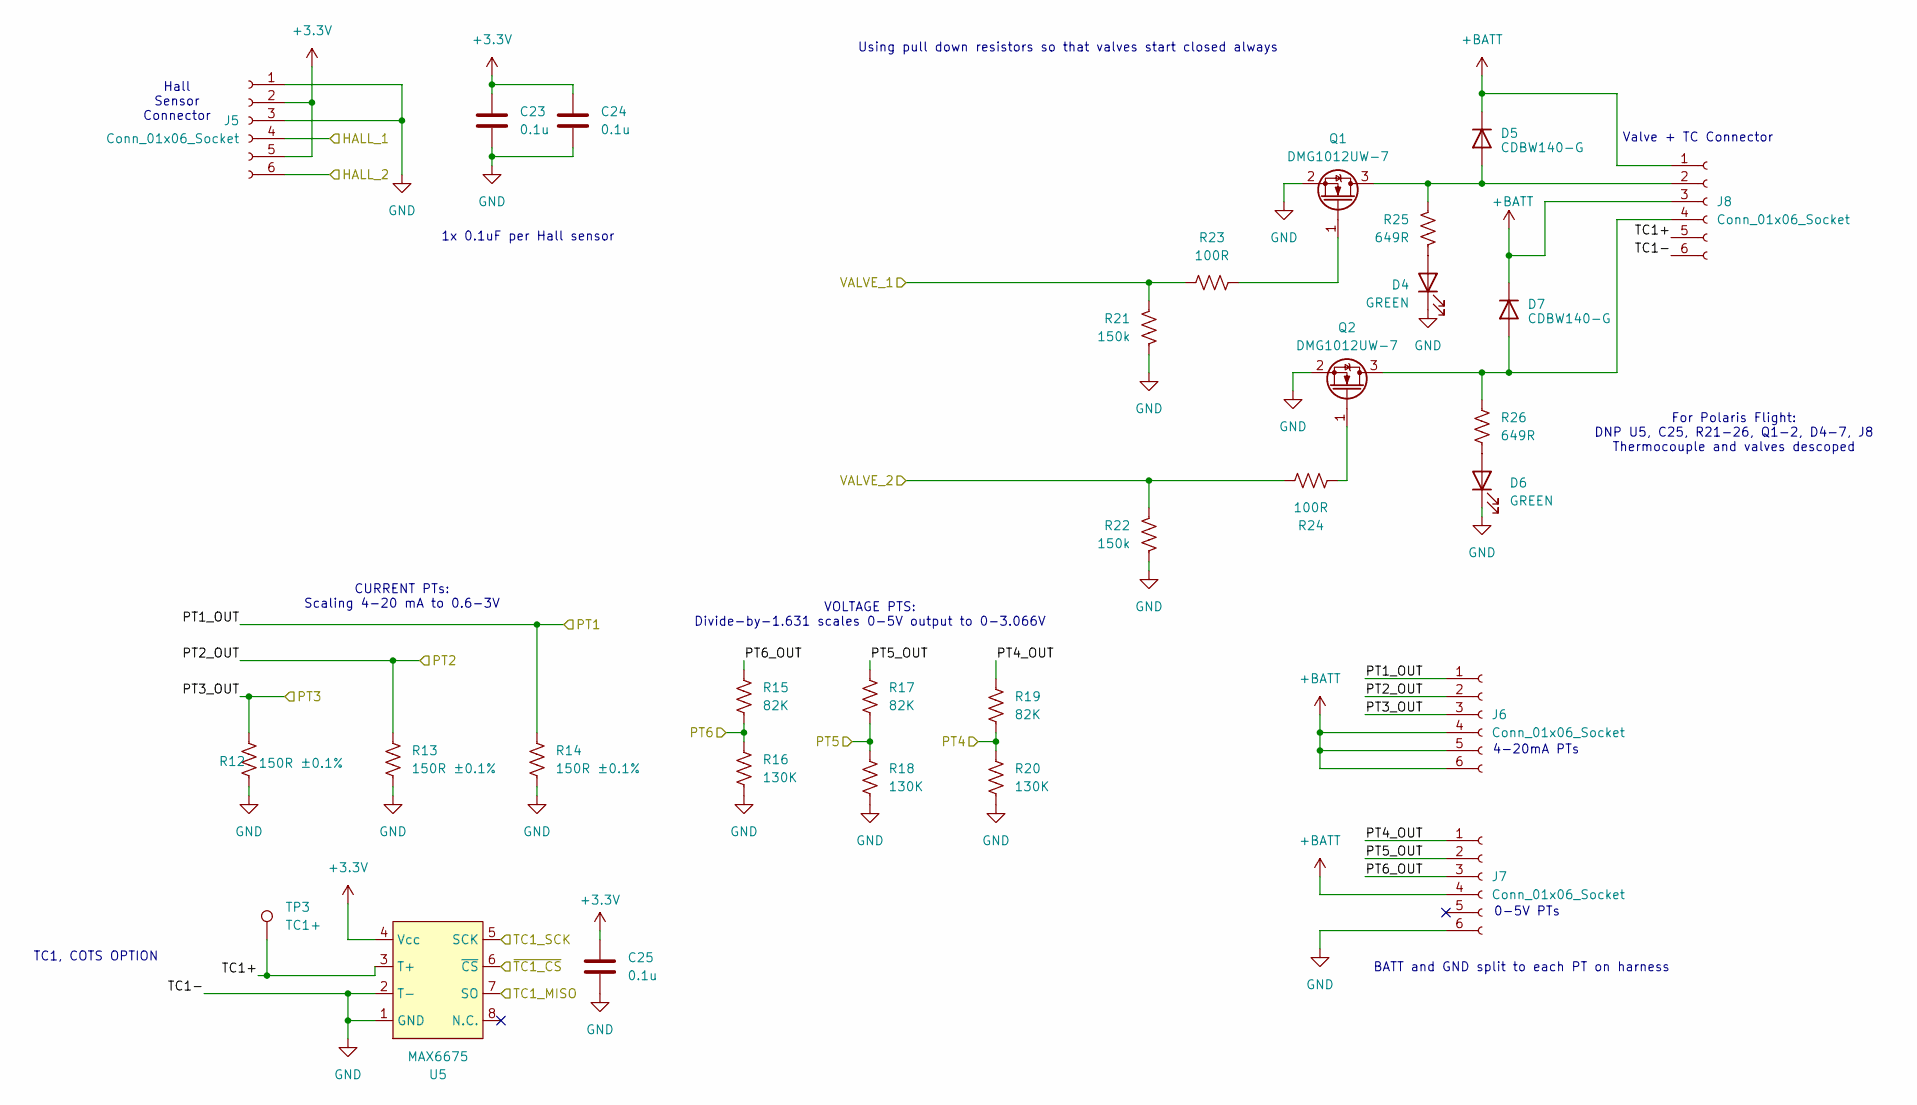
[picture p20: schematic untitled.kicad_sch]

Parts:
C23, C24, C25: 0.1u; C_0603_1608Metric_Pad1.08x0.95mm_HandSolder
D4, D6: GREEN; LED_1206_3216Metric_Pad1.42x1.75mm_HandSolder
D5, D7: CDBW140-G; D_SOD-123
J5, J6, J7, J8: Conn_01x06_Socket; connector_Harwin_G125–MG10605M4P
Q1, Q2: DMG1012UW-7; SOT_12UW-7_DIO
R12, R13, R14: 150R ±0.1%; R_0603_1608Metric_Pad0.98x0.95mm_HandSolder
R15, R17, R19: 82K; R_0603_1608Metric_Pad0.98x0.95mm_HandSolder
R16, R18, R20: 130K; R_0603_1608Metric_Pad0.98x0.95mm_HandSolder
R21, R22: 150k; R_0603_1608Metric_Pad0.98x0.95mm_HandSolder
R23, R24: 100R; R_0603_1608Metric_Pad0.98x0.95mm_HandSolder
R25, R26: 649R; R_0603_1608Metric_Pad0.98x0.95mm_HandSolder
TP3: TC1+; TestPoint_Pad_D2.0mm
U5: MAX6675; SOIC-8_3.9x4.9mm_P1.27mm

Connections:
+3.3V: C23.1, C24.1, C25.1, J5.2, J5.5, U5.4 (Vcc); also elsewhere on the board
+BATT: D5.1 (K), D7.1 (K), J6.4, J6.5, J6.6, J7.4, J8.1, J8.3; also elsewhere on the board
/MCU/HALL_1: J5.4; also elsewhere on the board
/MCU/HALL_2: J5.6; also elsewhere on the board
/MCU/PT4: R19.2, R20.1; also elsewhere on the board
/MCU/PT5: R17.2, R18.1; also elsewhere on the board
/MCU/PT6: R15.2, R16.1; also elsewhere on the board
/MCU/TC1_MISO: U5.7 (SO); also elsewhere on the board
/MCU/TC1_SCK: U5.5 (SCK); also elsewhere on the board
/MCU/VALVE_1: R21.2, R23.2; also elsewhere on the board
/MCU/VALVE_2: R22.1, R24.2; also elsewhere on the board
/MCU/~TC1_CS: U5.6 (~CS); also elsewhere on the board
/Valves and Sensors/PT1_OUT: J6.1, R14.1; also elsewhere on the board
/Valves and Sensors/PT2_OUT: J6.2, R13.1; also elsewhere on the board
/Valves and Sensors/PT3_OUT: J6.3, R12.1; also elsewhere on the board
/Valves and Sensors/PT4_OUT: J7.1, R19.1
/Valves and Sensors/PT5_OUT: J7.2, R17.1
/Valves and Sensors/PT6_OUT: J7.3, R15.1
/Valves and Sensors/TC1+: J8.5, TP3.1, U5.3 (T+); also elsewhere on the board
GND: C23.2, C24.2, C25.2, D4.1 (K), D6.1 (K), J5.1, J5.3, J7.6, J8.6, Q1.2 (S), Q2.2 (S), R12.2, R13.2, R14.2, R16.2, R18.2, R20.2, R21.1, R22.2, U5.1 (GND), U5.2 (T-); also elsewhere on the board
unnamed: D4.2 (A), R25.1
unnamed: D5.2 (A), J8.2, Q1.3 (D), R25.2
unnamed: D6.2 (A), R26.2
unnamed: D7.2 (A), J8.4, Q2.3 (D), R26.1
unnamed: Q1.1 (G), R23.1
unnamed: Q2.1 (G), R24.1

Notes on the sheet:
Hall Sensor Connector
0-5V PTs
Valve + TC Connector
1x 0.1uF per Hall sensor
CURRENT PTs: Scaling 4-20 mA to 0.6-3V
For Polaris Flight: DNP U5, C25, R21-26, Q1-2, D4-7, J8 Thermocouple and valves descoped
BATT and GND split to each PT on harness
Using pull down resistors so that valves start closed always
4-20mA PTs
TC1, COTS OPTION
VOLTAGE PTS: Divide-by-1.631 scales 0-5V output to 0-3.066V

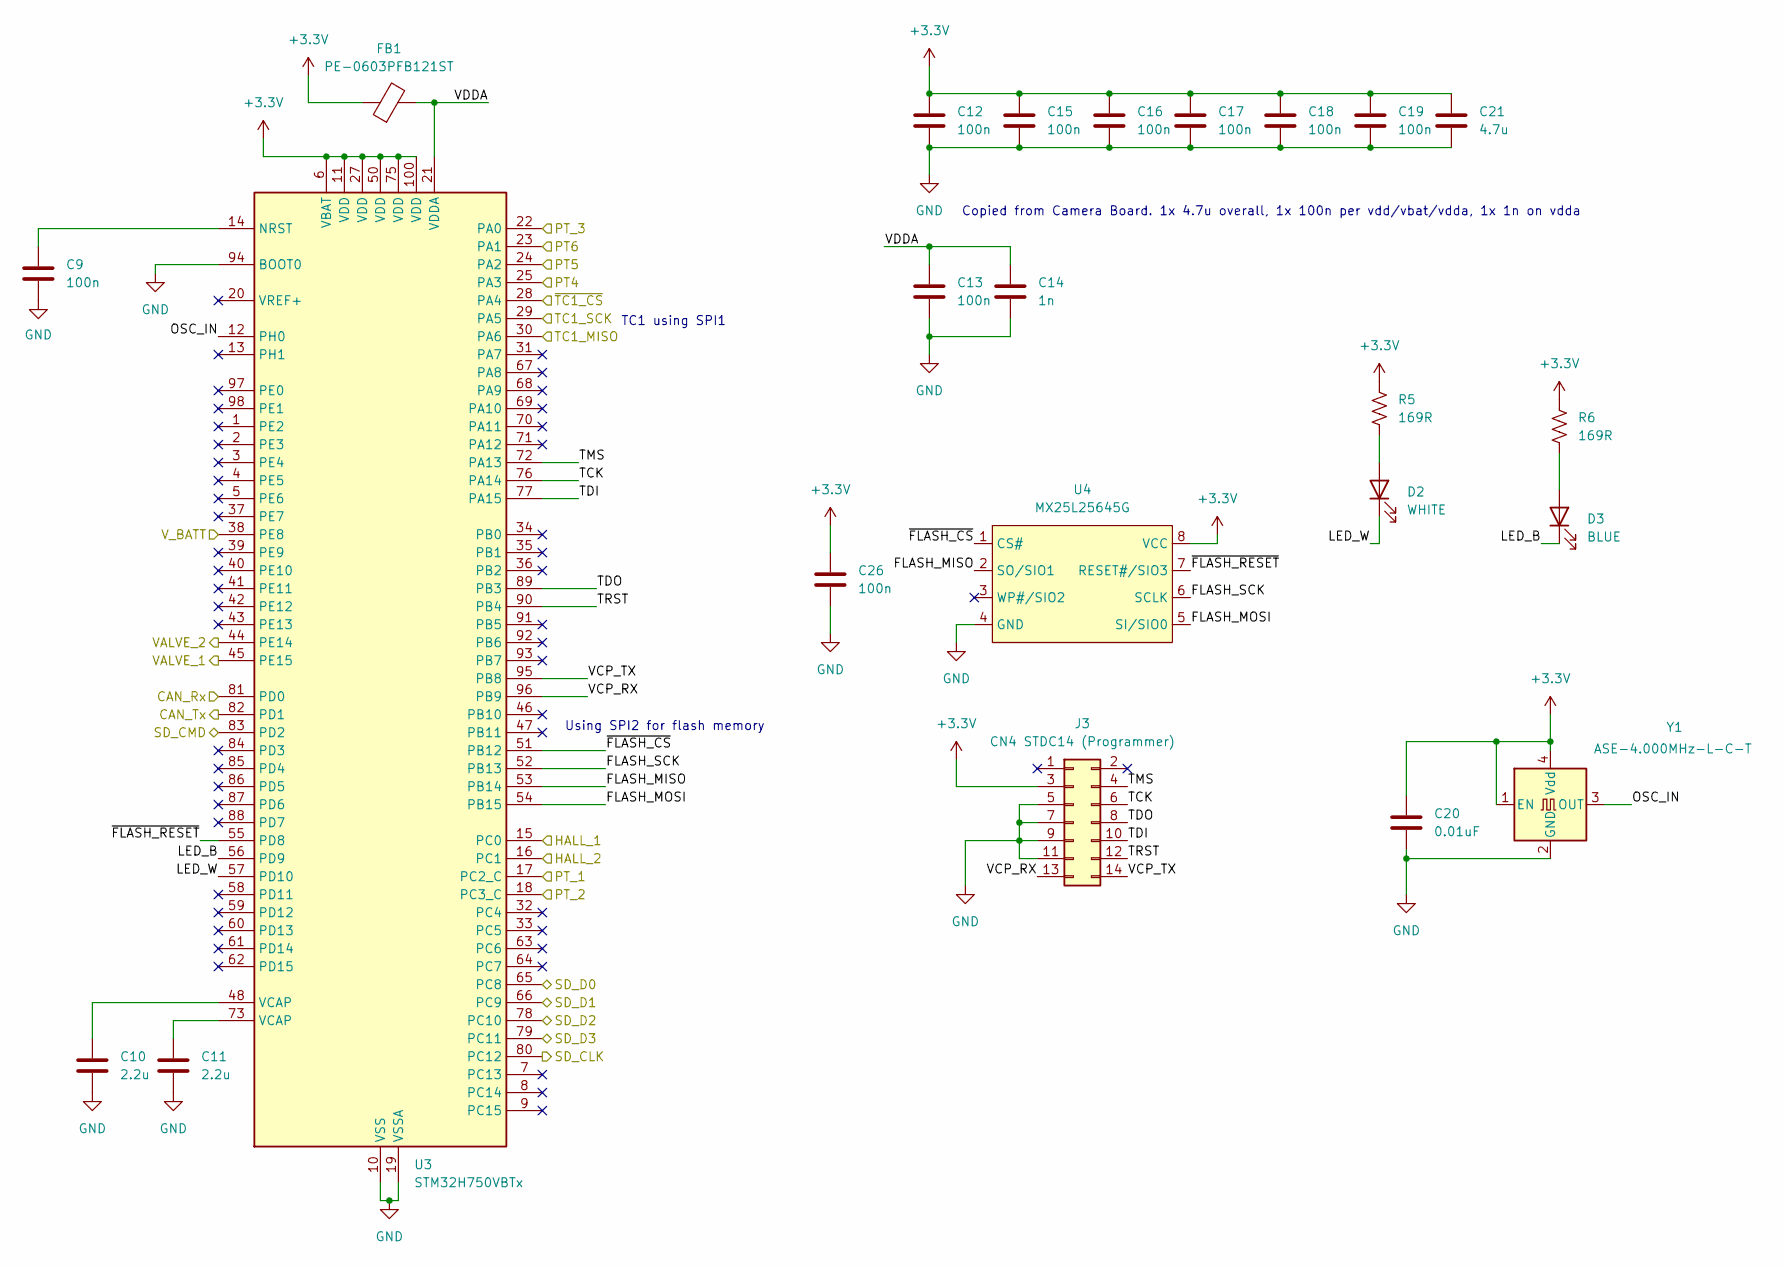
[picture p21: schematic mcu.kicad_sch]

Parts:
C9, C12, C13, C15, C16, C17, C18, C19, C26: 100n; C_0603_1608Metric_Pad1.08x0.95mm_HandSolder
C10, C11: 2.2u; C_0603_1608Metric_Pad1.08x0.95mm_HandSolder
C14: 1n; C_0603_1608Metric_Pad1.08x0.95mm_HandSolder
C20: 0.01uF; C_0603_1608Metric_Pad1.08x0.95mm_HandSolder
C21: 4.7u; C_0603_1608Metric_Pad1.08x0.95mm_HandSolder
D2: WHITE; LED_1206_3216Metric_Pad1.42x1.75mm_HandSolder
D3: BLUE; LED_1206_3216Metric_Pad1.42x1.75mm_HandSolder
FB1: PE-0603PFB121ST; R_0603_1608Metric_Pad0.98x0.95mm_HandSolder
J3: CN4 STDC14 (Programmer); PinSocket_2x07_P1.27mm_Vertical_SMD
R5, R6: 169R; R_0603_1608Metric_Pad0.98x0.95mm_HandSolder
U3: STM32H750VBTx; LQFP-100_14x14mm_P0.5mm
U4: MX25L25645G; SOIC-8_5.3x5.3mm_P1.27mm
Y1: ASE-4.000MHz-L-C-T; Oscillator_SMD_Abracon_ASE-4Pin_3.2x2.5mm

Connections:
+3.3V: C12.1, C15.1, C16.1, C17.1, C18.1, C19.1, C20.1, C21.1, C26.1, FB1.1, J3.3, R5.1, R6.1, U3.6 (VBAT), U3.11 (VDD), U3.27 (VDD), U3.50 (VDD), U3.75 (VDD), U3.100 (VDD), U4.8 (VCC), Y1.1 (EN), Y1.4 (Vdd); also elsewhere on the board
/CAN_Rx: U3.81 (PD0); also elsewhere on the board
/CAN_Tx: U3.82 (PD1); also elsewhere on the board
/MCU/FLASH_MISO: U3.53 (PB14), U4.2 (SO/SIO1)
/MCU/FLASH_MOSI: U3.54 (PB15), U4.5 (SI/SIO0)
/MCU/FLASH_SCK: U3.52 (PB13), U4.6 (SCLK)
/MCU/HALL_1: U3.15 (PC0); also elsewhere on the board
/MCU/HALL_2: U3.16 (PC1); also elsewhere on the board
/MCU/LED_B: D3.1 (K), U3.56 (PD9)
/MCU/LED_W: D2.1 (K), U3.57 (PD10)
/MCU/OSC_IN: U3.12 (PH0), Y1.3 (OUT)
/MCU/PT4: U3.25 (PA3); also elsewhere on the board
/MCU/PT5: U3.24 (PA2); also elsewhere on the board
/MCU/PT6: U3.23 (PA1); also elsewhere on the board
/MCU/SD_CLK: U3.80 (PC12); also elsewhere on the board
/MCU/SD_CMD: U3.83 (PD2); also elsewhere on the board
/MCU/SD_D0: U3.65 (PC8); also elsewhere on the board
/MCU/SD_D1: U3.66 (PC9); also elsewhere on the board
/MCU/SD_D2: U3.78 (PC10); also elsewhere on the board
/MCU/SD_D3: U3.79 (PC11); also elsewhere on the board
/MCU/TC1_MISO: U3.30 (PA6); also elsewhere on the board
/MCU/TC1_SCK: U3.29 (PA5); also elsewhere on the board
/MCU/TCK: J3.6, U3.76 (PA14)
/MCU/TDI: J3.10, U3.77 (PA15)
/MCU/TDO: J3.8, U3.89 (PB3)
/MCU/TMS: J3.4, U3.72 (PA13)
/MCU/TRST: J3.12, U3.90 (PB4)
/MCU/VALVE_1: U3.45 (PE15); also elsewhere on the board
/MCU/VALVE_2: U3.44 (PE14); also elsewhere on the board
/MCU/VCP_RX: J3.13, U3.96 (PB9)
/MCU/VCP_TX: J3.14, U3.95 (PB8)
/MCU/VDDA: C13.1, C14.1, FB1.2, U3.21 (VDDA)
/MCU/V_BATT: U3.38 (PE8); also elsewhere on the board
/MCU/~FLASH_CS: U3.51 (PB12), U4.1 (CS#)
/MCU/~FLASH_RESET: U3.55 (PD8), U4.7 (RESET#/SIO3)
/MCU/~TC1_CS: U3.28 (PA4); also elsewhere on the board
/Valves and Sensors/PT1_OUT: U3.17 (PC2_C); also elsewhere on the board
/Valves and Sensors/PT2_OUT: U3.18 (PC3_C); also elsewhere on the board
/Valves and Sensors/PT3_OUT: U3.22 (PA0); also elsewhere on the board
GND: C9.2, C10.2, C11.2, C12.2, C13.2, C14.2, C15.2, C16.2, C17.2, C18.2, C19.2, C20.2, C21.2, C26.2, J3.5, J3.7, J3.9, J3.11, U3.10 (VSS), U3.19 (VSSA), U3.26 (VSS), U3.49 (VSS), U3.74 (VSS), U3.94 (BOOT0), U3.99 (VSS), U4.4 (GND), Y1.2 (GND); also elsewhere on the board
unnamed: C10.1, U3.48 (VCAP)
unnamed: C11.1, U3.73 (VCAP)
unnamed: D2.2 (A), R5.2
unnamed: D3.2 (A), R6.2
unnamed: C9.1, U3.14 (NRST)

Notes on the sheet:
Using SPI2 for flash memory
TC1 using SPI1
Copied from Camera Board. 1x 4.7u overall, 1x 100n per vdd/vbat/vdda, 1x 1n on vdda

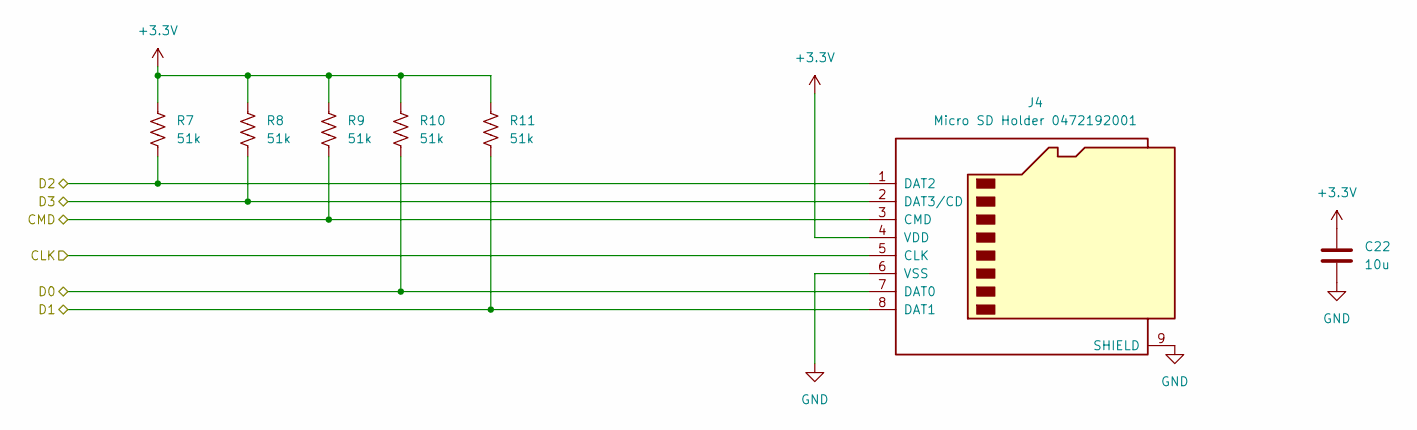
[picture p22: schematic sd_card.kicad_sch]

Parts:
C22: 10u; C_0603_1608Metric_Pad1.08x0.95mm_HandSolder
J4: Micro SD Holder 0472192001; microSD_HC_Molex_47219-2001
R7, R8, R9, R10, R11: 51k; R_0603_1608Metric_Pad0.98x0.95mm_HandSolder

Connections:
+3.3V: C22.1, J4.4 (VDD), R7.1, R8.1, R9.1, R10.1, R11.1; also elsewhere on the board
/MCU/SD_CLK: J4.5 (CLK); also elsewhere on the board
/MCU/SD_CMD: J4.3 (CMD), R9.2; also elsewhere on the board
/MCU/SD_D0: J4.7 (DAT0), R10.2; also elsewhere on the board
/MCU/SD_D1: J4.8 (DAT1), R11.2; also elsewhere on the board
/MCU/SD_D2: J4.1 (DAT2), R7.2; also elsewhere on the board
/MCU/SD_D3: J4.2 (DAT3/CD), R8.2; also elsewhere on the board
GND: C22.2, J4.6 (VSS), J4.9 (SHIELD); also elsewhere on the board

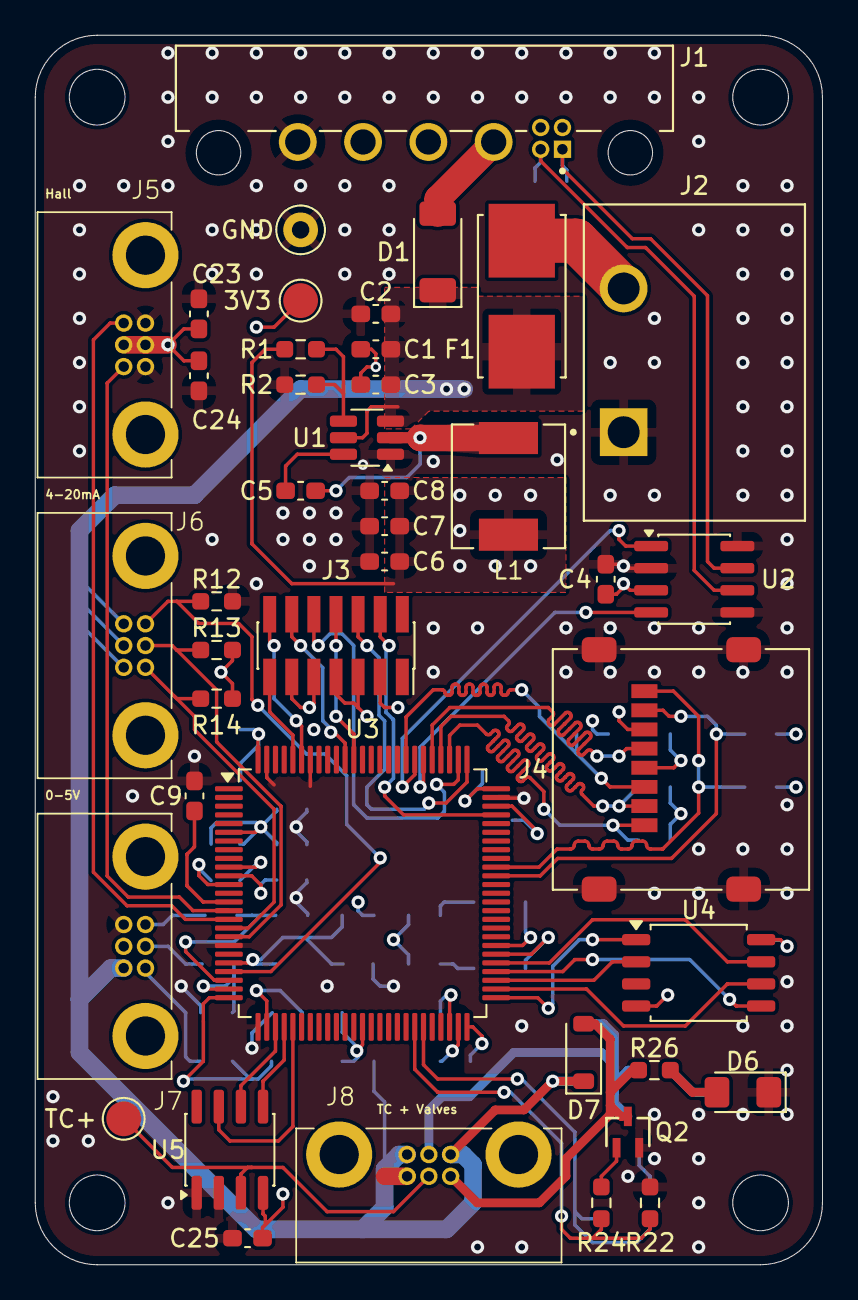
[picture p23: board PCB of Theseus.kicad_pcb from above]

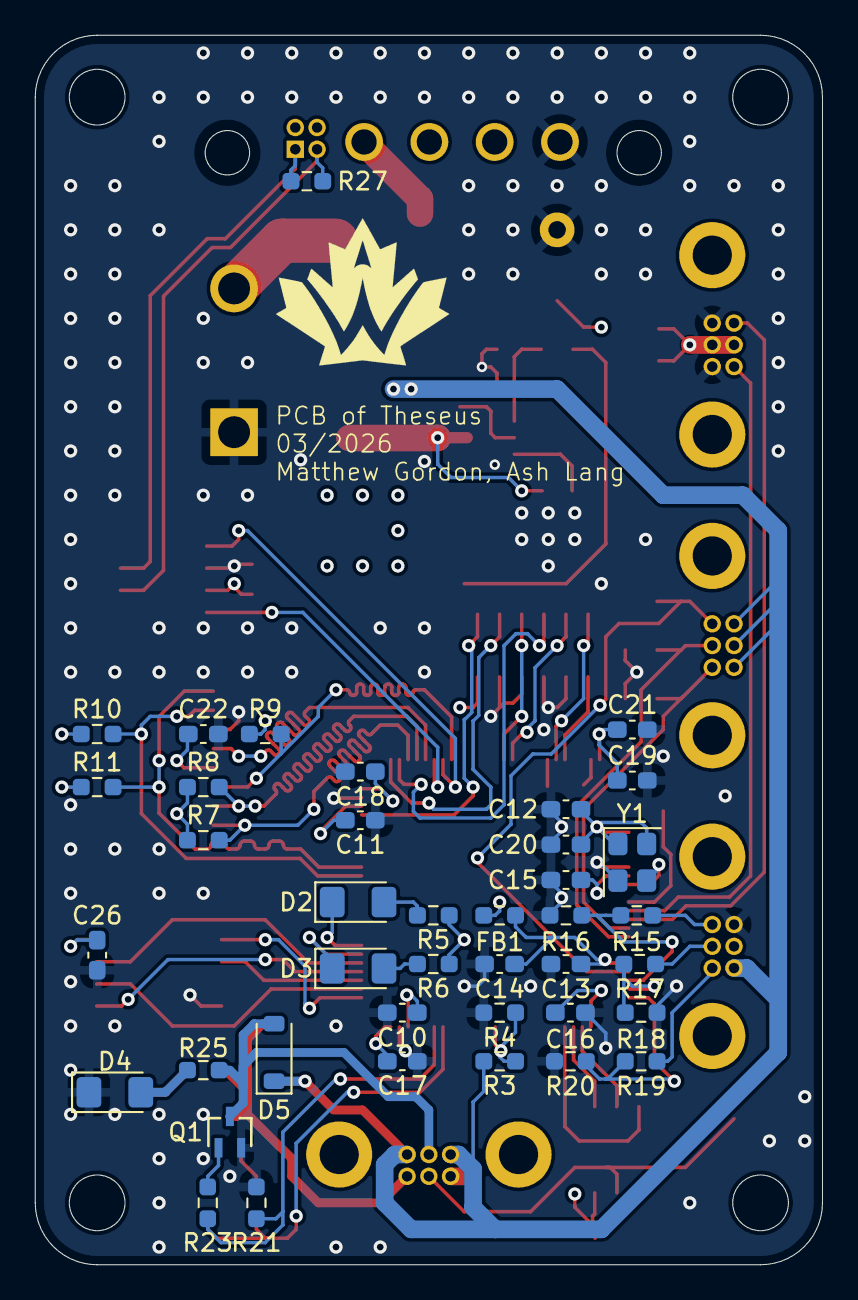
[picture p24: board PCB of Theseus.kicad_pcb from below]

Board: 4 copper layers, 45.2 x 70.6 mm, 86 parts (40 on the bottom side), 63 nets.

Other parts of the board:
3V3: TestPoint; TestPoint_Pad_D2.0mm
GND: TestPoint; TestPoint_Keystone_5000-5004_Miniature
TC+: TC1+; TestPoint_Pad_D2.0mm

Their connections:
+3.3V: 3V3.1; also elsewhere on the board
/Valves and Sensors/TC1+: TC+.1; also elsewhere on the board
GND: GND.1; also elsewhere on the board

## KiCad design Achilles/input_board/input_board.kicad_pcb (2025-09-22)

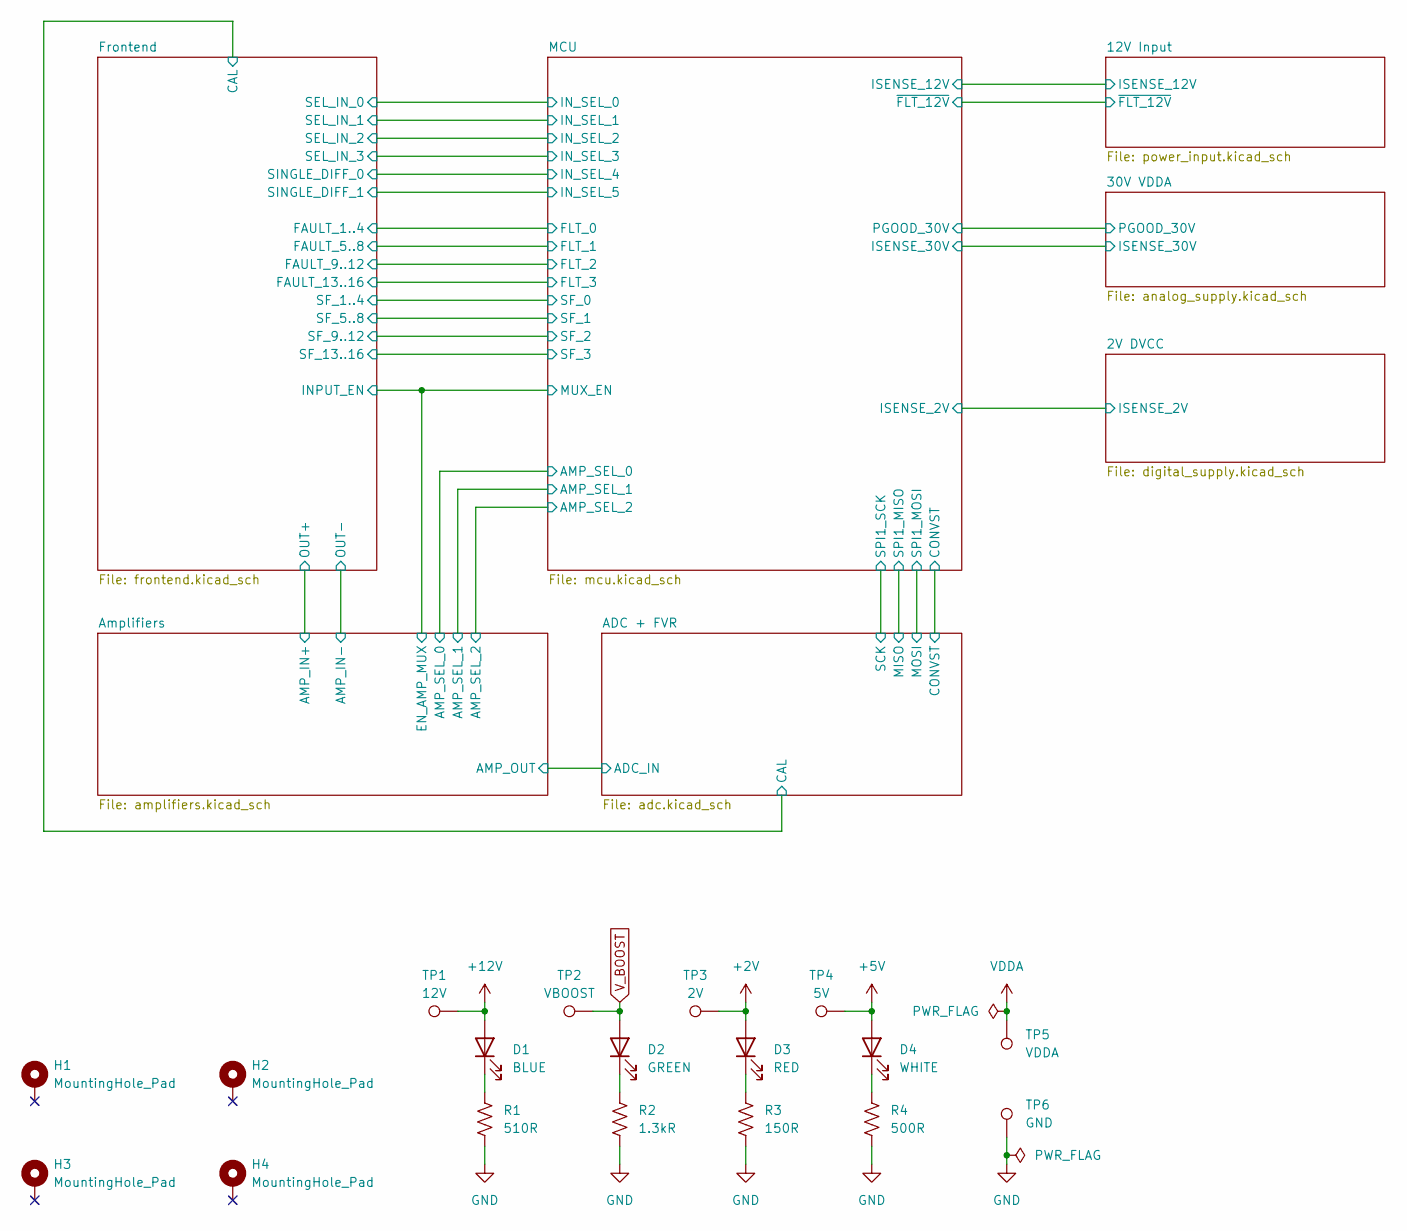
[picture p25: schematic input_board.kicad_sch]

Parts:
D1: BLUE; LED_1206_3216Metric_Pad1.42x1.75mm_HandSolder
D2: GREEN; LED_1206_3216Metric_Pad1.42x1.75mm_HandSolder
D3: RED; LED_1206_3216Metric_Pad1.42x1.75mm_HandSolder
D4: WHITE; LED_1206_3216Metric_Pad1.42x1.75mm_HandSolder
H1, H2, H3, H4: MountingHole_Pad; MountingHole_3.2mm_M3_DIN965_Pad
R1: 510R; R_0805_2012Metric_Pad1.20x1.40mm_HandSolder
R2: 1.3kR; R_0805_2012Metric_Pad1.20x1.40mm_HandSolder
R3: 150R; R_0805_2012Metric_Pad1.20x1.40mm_HandSolder
R4: 500R; R_0805_2012Metric_Pad1.20x1.40mm_HandSolder
TP1: 12V; TestPoint_Keystone_5000-5004_Miniature
TP2: VBOOST; TestPoint_Keystone_5000-5004_Miniature
TP3: 2V; TestPoint_Keystone_5000-5004_Miniature
TP4: 5V; TestPoint_Pad_1.5x1.5mm
TP5: VDDA; TestPoint_Keystone_5000-5004_Miniature
TP6: GND; TestPoint_Keystone_5000-5004_Miniature

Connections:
+2V: D3.2 (A), TP3.1; also elsewhere on the board
+5V: D4.2 (A), TP4.1; also elsewhere on the board
+12V: D1.2 (A), TP1.1; also elsewhere on the board
GND: R1.2, R2.2, R3.2, R4.2, TP6.1; also elsewhere on the board
unnamed: D1.1 (K), R1.1
unnamed: D2.1 (K), R2.1
unnamed: D3.1 (K), R3.1
unnamed: D4.1 (K), R4.1
VDDA: TP5.1; also elsewhere on the board
V_BOOST: D2.2 (A), TP2.1; also elsewhere on the board

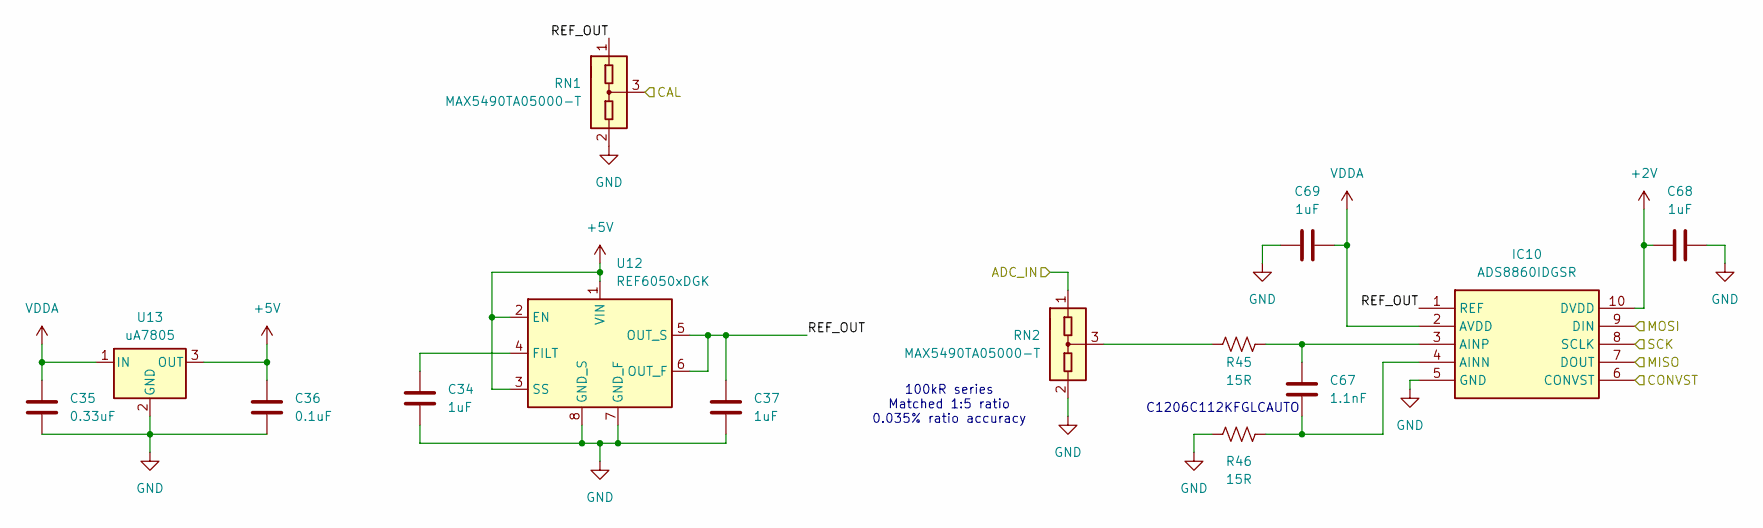
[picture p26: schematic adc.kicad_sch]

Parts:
C34, C37, C68, C69: 1uF; C_0805_2012Metric_Pad1.18x1.45mm_HandSolder
C35: 0.33uF; C_0805_2012Metric_Pad1.18x1.45mm_HandSolder
C36: 0.1uF; C_0805_2012Metric_Pad1.18x1.45mm_HandSolder
C67: 1.1nF; C_0805_2012Metric_Pad1.18x1.45mm_HandSolder
IC10: ADS8860IDGSR; SOP50P490X110-10N; Manufacturer_Part_Number ADS8860IDGSR; Mouser Part Number 595-ADS8860IDGSR
R45, R46: 15R; R_0805_2012Metric_Pad1.20x1.40mm_HandSolder
RN1, RN2: MAX5490TA05000-T; SOT-23
U12: REF6050xDGK; VSSOP-8_3x3mm_P0.65mm
U13: uA7805; TO-263-3_TabPin2

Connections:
+2V: C68.2, IC10.10 (DVDD); also elsewhere on the board
+5V: C36.1, U12.1 (VIN), U12.2 (EN), U12.3 (SS), U13.3 (OUT); also elsewhere on the board
/ADC + FVR/ADC_IN: RN2.1 (COM1); also elsewhere on the board
/ADC + FVR/CAL: RN1.3 (R2); also elsewhere on the board
/ADC + FVR/CONVST: IC10.6 (CONVST); also elsewhere on the board
/ADC + FVR/MISO: IC10.7 (DOUT); also elsewhere on the board
/ADC + FVR/MOSI: IC10.9 (DIN); also elsewhere on the board
/ADC + FVR/REF_OUT: C37.2, IC10.1 (REF), RN1.1 (COM1), U12.5 (OUT_S), U12.6 (OUT_F)
/ADC + FVR/SCK: IC10.8 (SCLK); also elsewhere on the board
GND: C34.1, C35.2, C36.2, C37.1, C68.1, C69.1, IC10.5 (GND), R46.2, RN1.2 (R1), RN2.2 (R1), U12.7 (GND_F), U12.8 (GND_S), U13.2 (GND); also elsewhere on the board
unnamed: C67.1, IC10.4 (AINN), R46.1
unnamed: C67.2, IC10.3 (AINP), R45.2
unnamed: R45.1, RN2.3 (R2)
unnamed: C34.2, U12.4 (FILT)
VDDA: C35.1, C69.2, IC10.2 (AVDD), U13.1 (IN); also elsewhere on the board

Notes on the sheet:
C1206C112KFGLCAUTO
100kR series Matched 1:5 ratio 0.035% ratio accuracy

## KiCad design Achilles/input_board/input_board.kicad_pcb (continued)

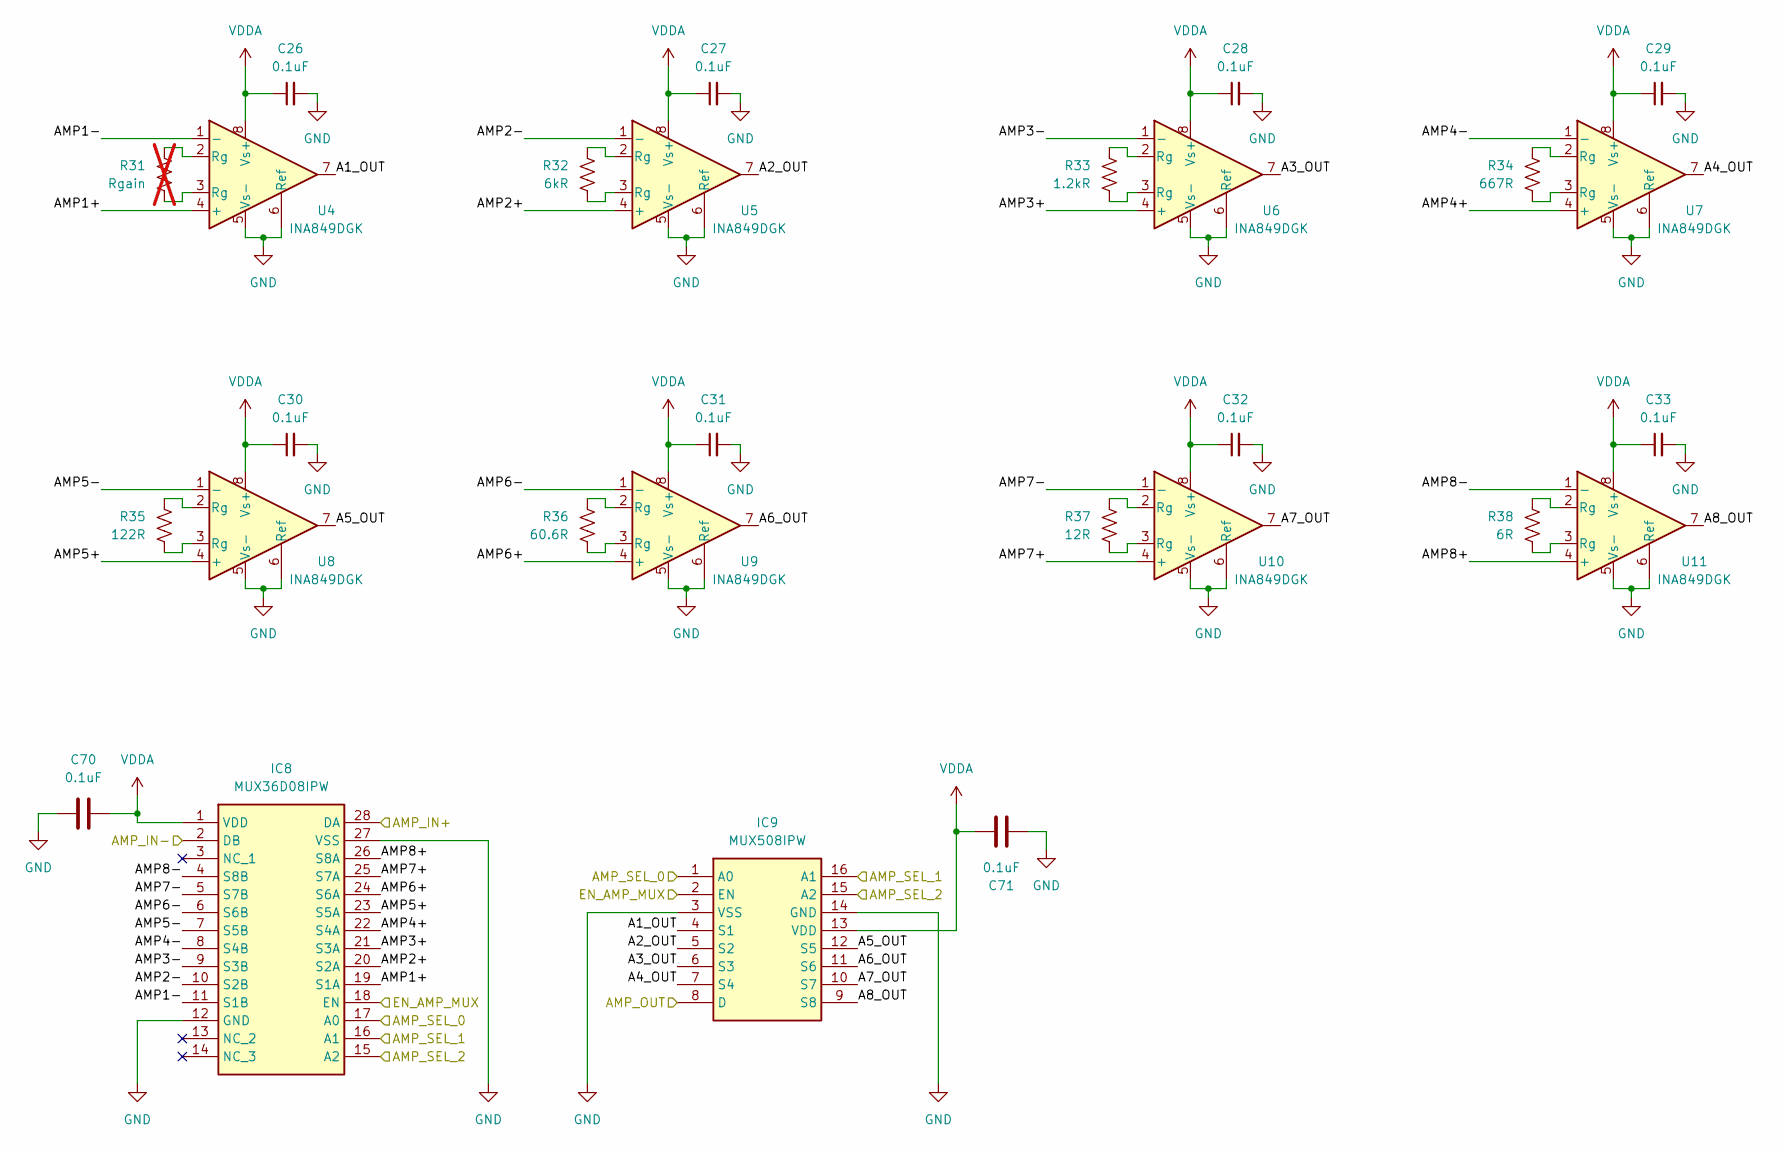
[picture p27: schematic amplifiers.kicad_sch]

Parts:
C26, C27, C28, C29, C30, C31, C32, C33, C70, C71: 0.1uF; C_0805_2012Metric_Pad1.18x1.45mm_HandSolder
IC8: MUX36D08IPW; SOP65P640X120-28N; Manufacturer_Part_Number MUX36D08IPW; Mouser Part Number 595-MUX36D08IPW
IC9: MUX508IPW; SOP65P640X120-16N; Manufacturer_Part_Number MUX508IPW; Mouser Part Number 595-MUX508IPW
R31: Rgain; not fitted
R32: 6kR; R_0805_2012Metric_Pad1.20x1.40mm_HandSolder
R33: 1.2kR; R_0805_2012Metric_Pad1.20x1.40mm_HandSolder
R34: 667R; R_0805_2012Metric_Pad1.20x1.40mm_HandSolder
R35: 122R; R_0805_2012Metric_Pad1.20x1.40mm_HandSolder
R36: 60.6R; R_0805_2012Metric_Pad1.20x1.40mm_HandSolder
R37: 12R; R_0805_2012Metric_Pad1.20x1.40mm_HandSolder
R38: 6R; R_0805_2012Metric_Pad1.20x1.40mm_HandSolder
U4, U5, U6, U7, U8, U9, U10, U11: INA849DGK; VSSOP-8_3x3mm_P0.65mm

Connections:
/ADC + FVR/ADC_IN: IC9.8 (D); also elsewhere on the board
/Amplifiers/A1_OUT: IC9.4 (S1), U4.7
/Amplifiers/A2_OUT: IC9.5 (S2), U5.7
/Amplifiers/A3_OUT: IC9.6 (S3), U6.7
/Amplifiers/A4_OUT: IC9.7 (S4), U7.7
/Amplifiers/A5_OUT: IC9.12 (S5), U8.7
/Amplifiers/A6_OUT: IC9.11 (S6), U9.7
/Amplifiers/A7_OUT: IC9.10 (S7), U10.7
/Amplifiers/A8_OUT: IC9.9 (S8), U11.7
/Amplifiers/AMP1+: IC8.19 (S1A), U4.4 (+)
/Amplifiers/AMP1-: IC8.11 (S1B), U4.1 (-)
/Amplifiers/AMP2+: IC8.20 (S2A), U5.4 (+)
/Amplifiers/AMP2-: IC8.10 (S2B), U5.1 (-)
/Amplifiers/AMP3+: IC8.21 (S3A), U6.4 (+)
/Amplifiers/AMP3-: IC8.9 (S3B), U6.1 (-)
/Amplifiers/AMP4+: IC8.22 (S4A), U7.4 (+)
/Amplifiers/AMP4-: IC8.8 (S4B), U7.1 (-)
/Amplifiers/AMP5+: IC8.23 (S5A), U8.4 (+)
/Amplifiers/AMP5-: IC8.7 (S5B), U8.1 (-)
/Amplifiers/AMP6+: IC8.24 (S6A), U9.4 (+)
/Amplifiers/AMP6-: IC8.6 (S6B), U9.1 (-)
/Amplifiers/AMP7+: IC8.25 (S7A), U10.4 (+)
/Amplifiers/AMP7-: IC8.5 (S7B), U10.1 (-)
/Amplifiers/AMP8+: IC8.26 (S8A), U11.4 (+)
/Amplifiers/AMP8-: IC8.4 (S8B), U11.1 (-)
/Amplifiers/AMP_IN+: IC8.28 (DA); also elsewhere on the board
/Amplifiers/AMP_IN-: IC8.2 (DB); also elsewhere on the board
/Amplifiers/AMP_SEL_0: IC8.17 (A0), IC9.1 (A0); also elsewhere on the board
/Amplifiers/AMP_SEL_1: IC8.16 (A1), IC9.16 (A1); also elsewhere on the board
/Amplifiers/AMP_SEL_2: IC8.15 (A2), IC9.15 (A2); also elsewhere on the board
/Frontend/EN_1..4: IC8.18 (EN), IC9.2 (EN); also elsewhere on the board
GND: C26.2, C27.2, C28.2, C29.2, C30.2, C31.2, C32.2, C33.2, C70.1, C71.1, IC8.12 (GND), IC8.27 (VSS), IC9.3 (VSS), IC9.14 (GND), U4.5 (Vs-), U4.6 (Ref), U5.5 (Vs-), U5.6 (Ref), U6.5 (Vs-), U6.6 (Ref), U7.5 (Vs-), U7.6 (Ref), U8.5 (Vs-), U8.6 (Ref), U9.5 (Vs-), U9.6 (Ref), U10.5 (Vs-), U10.6 (Ref), U11.5 (Vs-), U11.6 (Ref); also elsewhere on the board
unnamed: R32.1, U5.2 (Rg)
unnamed: R32.2, U5.3 (Rg)
unnamed: R33.1, U6.2 (Rg)
unnamed: R33.2, U6.3 (Rg)
unnamed: R34.1, U7.2 (Rg)
unnamed: R34.2, U7.3 (Rg)
unnamed: R35.1, U8.2 (Rg)
unnamed: R35.2, U8.3 (Rg)
unnamed: R36.1, U9.2 (Rg)
unnamed: R36.2, U9.3 (Rg)
unnamed: R37.1, U10.2 (Rg)
unnamed: R37.2, U10.3 (Rg)
unnamed: R38.1, U11.2 (Rg)
unnamed: R38.2, U11.3 (Rg)
unnamed: R31.1, U4.2 (Rg)
unnamed: R31.2, U4.3 (Rg)
VDDA: C26.1, C27.1, C28.1, C29.1, C30.1, C31.1, C32.1, C33.1, C70.2, C71.2, IC8.1 (VDD), IC9.13 (VDD), U4.8 (Vs+), U5.8 (Vs+), U6.8 (Vs+), U7.8 (Vs+), U8.8 (Vs+), U9.8 (Vs+), U10.8 (Vs+), U11.8 (Vs+); also elsewhere on the board

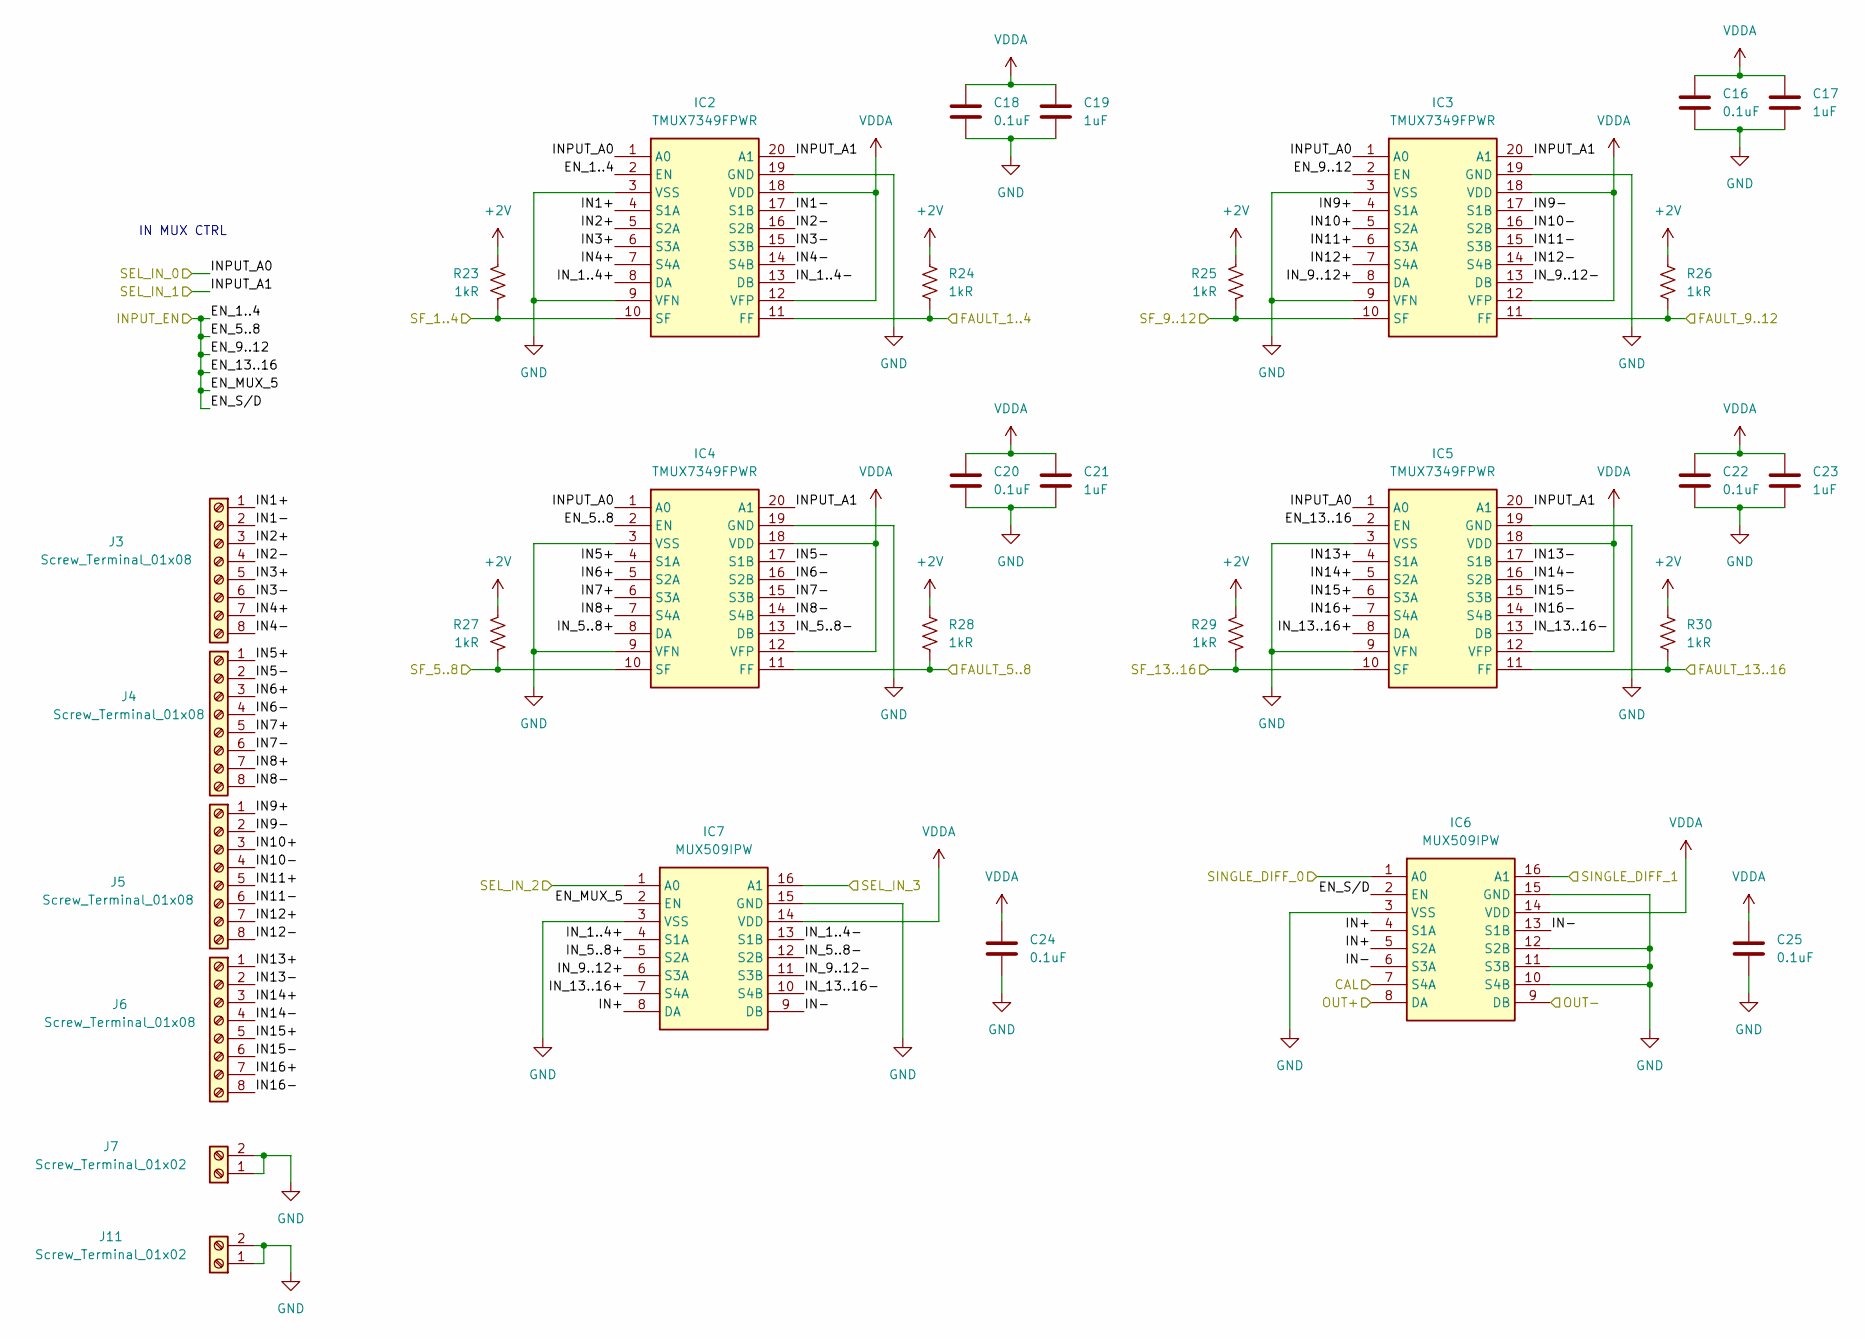
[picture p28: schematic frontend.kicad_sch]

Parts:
C16, C18, C20, C22, C24, C25: 0.1uF; C_0805_2012Metric_Pad1.18x1.45mm_HandSolder
C17, C19, C21, C23: 1uF; C_0805_2012Metric_Pad1.18x1.45mm_HandSolder
IC2, IC3, IC4, IC5: TMUX7349FPWR; SOP65P640X120-20N; Manufacturer_Part_Number TMUX7348FPWR; Mouser Part Number 595-TMUX7348FPWR
IC6, IC7: MUX509IPW; SOP65P640X120-16N; Manufacturer_Part_Number MUX509IPW; Mouser Part Number 595-MUX509IPW
J3, J4, J5, J6: Screw_Terminal_01x08; TerminalBlock_Phoenix_MPT-0,5-8-2.54_1x08_P2.54mm_Horizontal
J7, J11: Screw_Terminal_01x02; TerminalBlock_Phoenix_MPT-0,5-2-2.54_1x02_P2.54mm_Horizontal
R23, R24, R25, R26, R27, R28, R29, R30: 1kR; R_0805_2012Metric_Pad1.20x1.40mm_HandSolder

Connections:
+2V: R23.2, R24.2, R25.2, R26.2, R27.2, R28.2, R29.2, R30.2; also elsewhere on the board
/ADC + FVR/CAL: IC6.7 (S4A); also elsewhere on the board
/Amplifiers/AMP_IN+: IC6.8 (DA); also elsewhere on the board
/Amplifiers/AMP_IN-: IC6.9 (DB); also elsewhere on the board
/Frontend/EN_1..4: IC2.2 (EN), IC3.2 (EN), IC4.2 (EN), IC5.2 (EN), IC6.2 (EN), IC7.2 (EN); also elsewhere on the board
/Frontend/FAULT_1..4: IC2.11 (FF), R24.1; also elsewhere on the board
/Frontend/FAULT_5..8: IC4.11 (FF), R28.1; also elsewhere on the board
/Frontend/FAULT_9..12: IC3.11 (FF), R26.1; also elsewhere on the board
/Frontend/FAULT_13..16: IC5.11 (FF), R30.1; also elsewhere on the board
/Frontend/IN1+: IC2.4 (S1A), J3.1
/Frontend/IN1-: IC2.17 (S1B), J3.2
/Frontend/IN2+: IC2.5 (S2A), J3.3
/Frontend/IN2-: IC2.16 (S2B), J3.4
/Frontend/IN3+: IC2.6 (S3A), J3.5
/Frontend/IN3-: IC2.15 (S3B), J3.6
/Frontend/IN4+: IC2.7 (S4A), J3.7
/Frontend/IN4-: IC2.14 (S4B), J3.8
/Frontend/IN5+: IC4.4 (S1A), J4.1
/Frontend/IN5-: IC4.17 (S1B), J4.2
/Frontend/IN6+: IC4.5 (S2A), J4.3
/Frontend/IN6-: IC4.16 (S2B), J4.4
/Frontend/IN7+: IC4.6 (S3A), J4.5
/Frontend/IN7-: IC4.15 (S3B), J4.6
/Frontend/IN8+: IC4.7 (S4A), J4.7
/Frontend/IN8-: IC4.14 (S4B), J4.8
/Frontend/IN9+: IC3.4 (S1A), J5.1
/Frontend/IN9-: IC3.17 (S1B), J5.2
/Frontend/IN10+: IC3.5 (S2A), J5.3
/Frontend/IN10-: IC3.16 (S2B), J5.4
/Frontend/IN11+: IC3.6 (S3A), J5.5
/Frontend/IN11-: IC3.15 (S3B), J5.6
/Frontend/IN12+: IC3.7 (S4A), J5.7
/Frontend/IN12-: IC3.14 (S4B), J5.8
/Frontend/IN13+: IC5.4 (S1A), J6.1
/Frontend/IN13-: IC5.17 (S1B), J6.2
/Frontend/IN14+: IC5.5 (S2A), J6.3
/Frontend/IN14-: IC5.16 (S2B), J6.4
/Frontend/IN15+: IC5.6 (S3A), J6.5
/Frontend/IN15-: IC5.15 (S3B), J6.6
/Frontend/IN16+: IC5.7 (S4A), J6.7
/Frontend/IN16-: IC5.14 (S4B), J6.8
/Frontend/IN+: IC6.4 (S1A), IC6.5 (S2A), IC7.8 (DA)
/Frontend/IN-: IC6.6 (S3A), IC6.13 (S1B), IC7.9 (DB)
/Frontend/INPUT_A0: IC2.1 (A0), IC3.1 (A0), IC4.1 (A0), IC5.1 (A0); also elsewhere on the board
/Frontend/INPUT_A1: IC2.20 (A1), IC3.20 (A1), IC4.20 (A1), IC5.20 (A1); also elsewhere on the board
/Frontend/IN_1..4+: IC2.8 (DA), IC7.4 (S1A)
/Frontend/IN_1..4-: IC2.13 (DB), IC7.13 (S1B)
/Frontend/IN_5..8+: IC4.8 (DA), IC7.5 (S2A)
/Frontend/IN_5..8-: IC4.13 (DB), IC7.12 (S2B)
/Frontend/IN_9..12+: IC3.8 (DA), IC7.6 (S3A)
/Frontend/IN_9..12-: IC3.13 (DB), IC7.11 (S3B)
/Frontend/IN_13..16+: IC5.8 (DA), IC7.7 (S4A)
/Frontend/IN_13..16-: IC5.13 (DB), IC7.10 (S4B)
/Frontend/SEL_IN_2: IC7.1 (A0); also elsewhere on the board
/Frontend/SEL_IN_3: IC7.16 (A1); also elsewhere on the board
/Frontend/SF_1..4: IC2.10 (SF), R23.1; also elsewhere on the board
/Frontend/SF_5..8: IC4.10 (SF), R27.1; also elsewhere on the board
/Frontend/SF_9..12: IC3.10 (SF), R25.1; also elsewhere on the board
/Frontend/SF_13..16: IC5.10 (SF), R29.1; also elsewhere on the board
/Frontend/SINGLE_DIFF_0: IC6.1 (A0); also elsewhere on the board
/Frontend/SINGLE_DIFF_1: IC6.16 (A1); also elsewhere on the board
GND: C16.2, C17.2, C18.2, C19.2, C20.2, C21.2, C22.2, C23.2, C24.2, C25.2, IC2.3 (VSS), IC2.9 (VFN), IC2.19 (GND), IC3.3 (VSS), IC3.9 (VFN), IC3.19 (GND), IC4.3 (VSS), IC4.9 (VFN), IC4.19 (GND), IC5.3 (VSS), IC5.9 (VFN), IC5.19 (GND), IC6.3 (VSS), IC6.10 (S4B), IC6.11 (S3B), IC6.12 (S2B), IC6.15 (GND), IC7.3 (VSS), IC7.15 (GND), J7.1, J7.2, J11.1, J11.2; also elsewhere on the board
VDDA: C16.1, C17.1, C18.1, C19.1, C20.1, C21.1, C22.1, C23.1, C24.1, C25.1, IC2.12 (VFP), IC2.18 (VDD), IC3.12 (VFP), IC3.18 (VDD), IC4.12 (VFP), IC4.18 (VDD), IC5.12 (VFP), IC5.18 (VDD), IC6.14 (VDD), IC7.14 (VDD); also elsewhere on the board

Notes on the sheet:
IN MUX CTRL

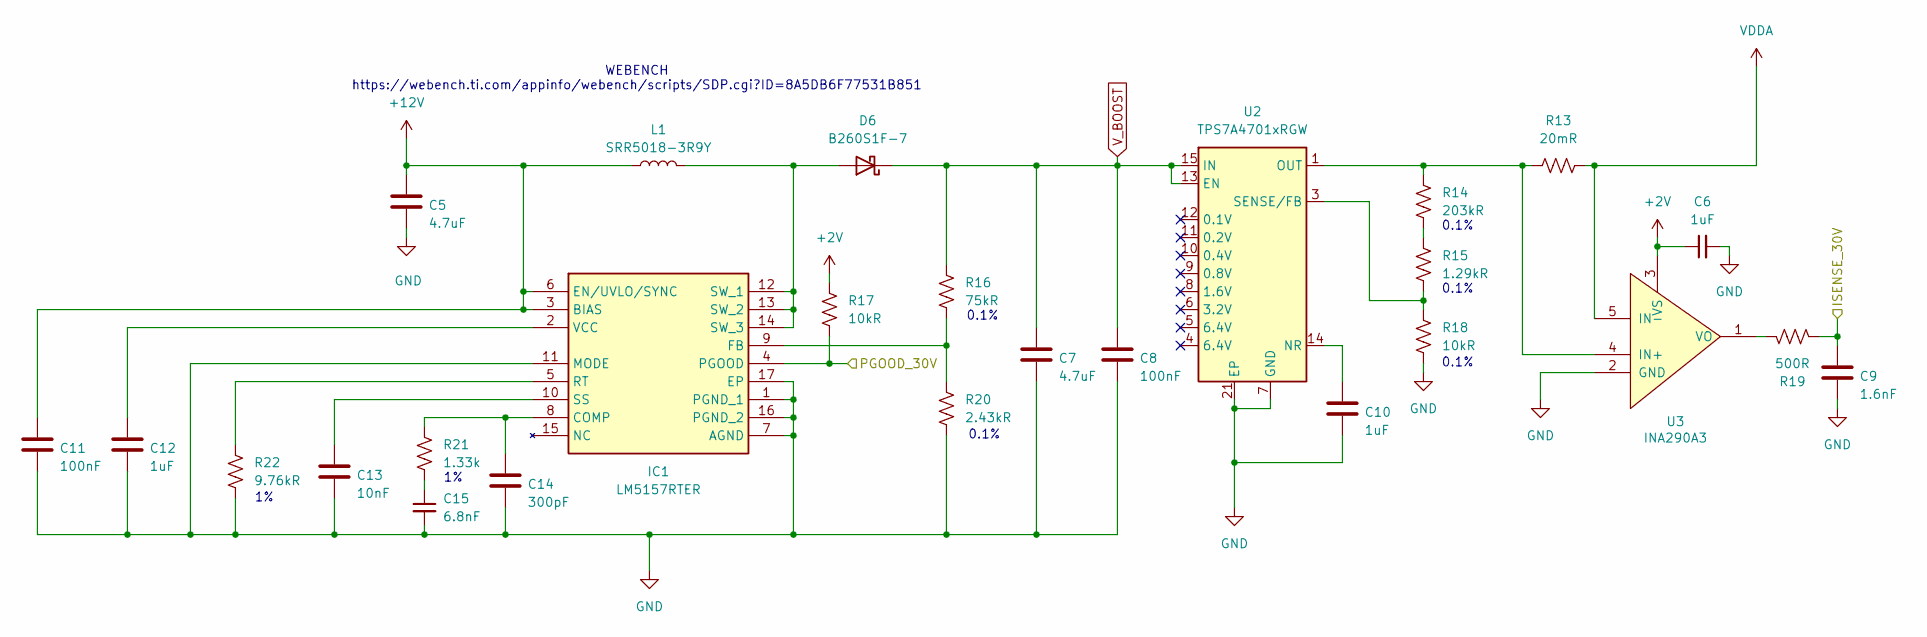
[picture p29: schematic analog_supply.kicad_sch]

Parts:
C5, C7: 4.7uF; C_0805_2012Metric_Pad1.18x1.45mm_HandSolder
C6, C10, C12: 1uF; C_0805_2012Metric_Pad1.18x1.45mm_HandSolder
C8, C11: 100nF; C_0805_2012Metric_Pad1.18x1.45mm_HandSolder
C9: 1.6nF; C_0805_2012Metric_Pad1.18x1.45mm_HandSolder
C13: 10nF; C_0805_2012Metric_Pad1.18x1.45mm_HandSolder
C14: 300pF; C_0805_2012Metric_Pad1.18x1.45mm_HandSolder
C15: 6.8nF; C_0805_2012Metric_Pad1.18x1.45mm_HandSolder
D6: B260S1F-7; CR_SOD123F_DIO
IC1: LM5157RTER; QFN50P300X300X80-17N-D; Manufacturer_Part_Number LM5157RTER; Mouser Part Number 595-LM5157RTER
L1: SRR5018-3R9Y; IND_BOURNS_SRR5018
R13: 20mR; R_0805_2012Metric_Pad1.20x1.40mm_HandSolder
R14: 203kR; R_0805_2012Metric_Pad1.20x1.40mm_HandSolder
R15: 1.29kR; R_0805_2012Metric_Pad1.20x1.40mm_HandSolder
R16: 75kR; R_0805_2012Metric_Pad1.20x1.40mm_HandSolder
R17, R18: 10kR; R_0805_2012Metric_Pad1.20x1.40mm_HandSolder
R19: 500R; R_0805_2012Metric_Pad1.20x1.40mm_HandSolder
R20: 2.43kR; R_0805_2012Metric_Pad1.20x1.40mm_HandSolder
R21: 1.33k; R_0805_2012Metric_Pad1.20x1.40mm_HandSolder
R22: 9.76kR; R_0805_2012Metric_Pad1.20x1.40mm_HandSolder
U2: TPS7A4701xRGW; Texas_RGW0020A_VQFN-20-1EP_5x5mm_P0.65mm_EP3.15x3.15mm_Ther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
U3: INA290A3; SC70-5_DCK_TEX

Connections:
+2V: C6.1, R17.1, U3.3 (VS); also elsewhere on the board
+12V: C5.1, C11.1, IC1.3 (BIAS), IC1.6 (EN/UVLO/SYNC), L1.1; also elsewhere on the board
/30V VDDA/ISENSE_30V: C9.1, R19.1; also elsewhere on the board
/30V VDDA/PGOOD_30V: IC1.4 (PGOOD), R17.2; also elsewhere on the board
GND: C5.2, C6.2, C7.2, C8.2, C9.2, C10.2, C11.2, C12.2, C13.2, C14.2, C15.2, IC1.1 (PGND_1), IC1.7 (AGND), IC1.11 (MODE), IC1.16 (PGND_2), IC1.17 (EP), R18.2, R20.2, R22.1, U2.7 (GND), U2.21 (EP), U3.2 (GND); also elsewhere on the board
unnamed: C15.1, R21.1
unnamed: D6.2 (A), IC1.12 (SW_1), IC1.13 (SW_2), IC1.14 (SW_3), L1.2
unnamed: C14.1, IC1.8 (COMP), R21.2
unnamed: IC1.9 (FB), R16.2, R20.1
unnamed: IC1.5 (RT), R22.2
unnamed: C13.1, IC1.10 (SS)
unnamed: C12.1, IC1.2 (VCC)
unnamed: R14.2, R15.1
unnamed: C10.1, U2.14 (NR)
unnamed: R15.2, R18.1, U2.3 (SENSE/FB)
unnamed: R13.1, R14.1, U2.1 (OUT), U2.20 (OUT), U3.4 (IN+)
unnamed: R19.2, U3.1 (VO)
VDDA: R13.2, U3.5 (IN-); also elsewhere on the board
V_BOOST: C7.1, C8.1, D6.1 (K), R16.1, U2.13 (EN), U2.15 (IN), U2.16 (IN); also elsewhere on the board

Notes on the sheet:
0.1%
WEBENCH https://webench.ti.com/appinfo/webench/scripts/SDP.cgi?ID=8A5DB6F77531B851

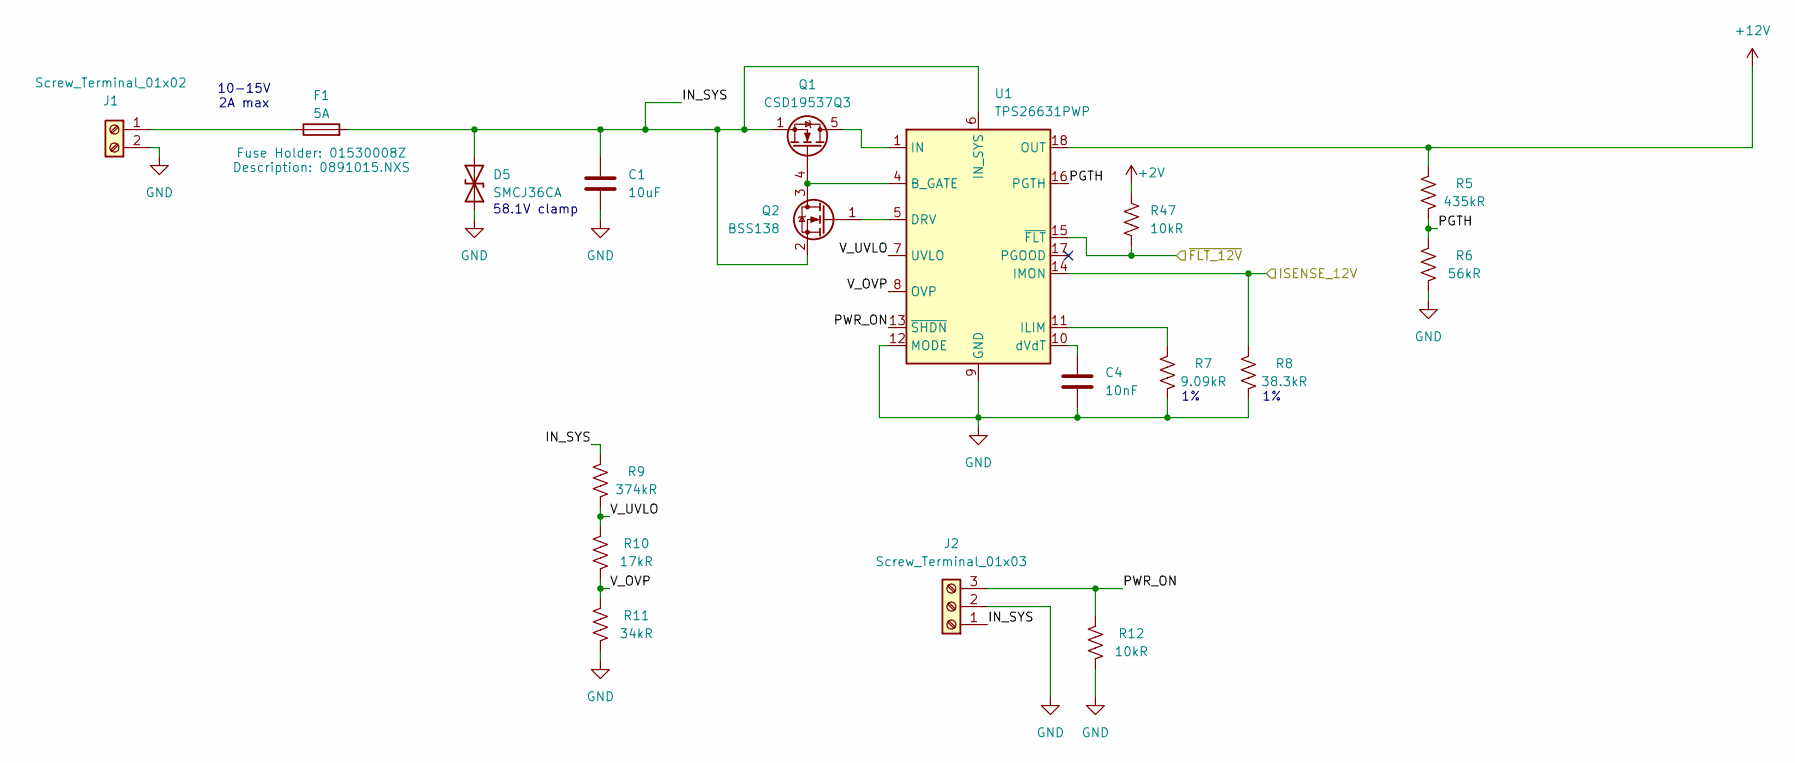
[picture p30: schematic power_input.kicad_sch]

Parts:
C1: 10uF; C_0805_2012Metric_Pad1.18x1.45mm_HandSolder
C4: 10nF; C_0805_2012Metric_Pad1.18x1.45mm_HandSolder
D5: SMCJ36CA; D_SMC_Handsoldering
F1: 5A; 01530009Z
J1: Screw_Terminal_01x02; TerminalBlock_Phoenix_MKDS-1,5-2-5.08_1x02_P5.08mm_Horizont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
J2: Screw_Terminal_01x03; PinHeader_1x03_P2.54mm_Vertical
Q1: CSD19537Q3; VSON-8_3.3x3.3mm_P0.65mm_NexFET
Q2: BSS138; SOT-23
R5: 435kR; R_0805_2012Metric_Pad1.20x1.40mm_HandSolder
R6: 56kR; R_0805_2012Metric_Pad1.20x1.40mm_HandSolder
R7: 9.09kR; R_0805_2012Metric_Pad1.20x1.40mm_HandSolder
R8: 38.3kR; R_0805_2012Metric_Pad1.20x1.40mm_HandSolder
R9: 374kR; R_0805_2012Metric_Pad1.20x1.40mm_HandSolder
R10: 17kR; R_0805_2012Metric_Pad1.20x1.40mm_HandSolder
R11: 34kR; R_0805_2012Metric_Pad1.20x1.40mm_HandSolder
R12, R47: 10kR; R_0805_2012Metric_Pad1.20x1.40mm_HandSolder
U1: TPS26631PWP; HTSSOP-20-1EP_4.4x6.5mm_P0.65mm_EP3.4x6.5mm_Mask2.96x2.96mm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

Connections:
+2V: R47.1; also elsewhere on the board
+12V: R5.1, U1.18 (OUT), U1.19 (OUT), U1.20 (OUT); also elsewhere on the board
/12V Input/IN_SYS: C1.1, D5.2 (A2), F1.2, J2.1, Q1.1 (S), Q1.2 (S), Q1.3 (S), Q2.2 (S), R9.1, U1.6 (IN_SYS)
/12V Input/ISENSE_12V: R8.1, U1.14 (IMON); also elsewhere on the board
/12V Input/PGTH: R5.2, R6.1, U1.16 (PGTH)
/12V Input/PWR_ON: J2.3, R12.1, U1.13 (~SHDN)
/12V Input/V_OVP: R10.2, R11.1, U1.8 (OVP)
/12V Input/V_UVLO: R9.2, R10.1, U1.7 (UVLO)
/12V Input/~FLT_12V: R47.2, U1.15 (~FLT); also elsewhere on the board
GND: C1.2, C4.2, D5.1 (A1), J1.2, J2.2, R6.2, R7.2, R8.2, R11.2, R12.2, U1.9 (GND), U1.12 (MODE), U1.21 (GND); also elsewhere on the board
unnamed: F1.1, J1.1
unnamed: Q1.5 (D), U1.1 (IN), U1.2 (IN), U1.3 (IN)
unnamed: Q1.4 (G), Q2.3 (D), U1.4 (B_GATE)
unnamed: Q2.1 (G), U1.5 (DRV)
unnamed: R7.1, U1.11 (ILIM)
unnamed: C4.1, U1.10 (dVdT)

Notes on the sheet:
10-15V 2A max
58.1V clamp


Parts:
C58, C61: 100nF; C_0805_2012Metric_Pad1.18x1.45mm_HandSolder
C59, C60: 10uF; C_0805_2012Metric_Pad1.18x1.45mm_HandSolder
C62, C63, C64: 22uF; C_0805_2012Metric_Pad1.18x1.45mm_HandSolder
C65: 1uF; C_0805_2012Metric_Pad1.18x1.45mm_HandSolder
C66: 1.6nF; C_0805_2012Metric_Pad1.18x1.45mm_HandSolder
L2: SRP1265A-2R2M; IND_SRP1265A-2R2M
R41: 20mR; R_0805_2012Metric_Pad1.20x1.40mm_HandSolder
R42: 17.4kR; R_0805_2012Metric_Pad1.20x1.40mm_HandSolder
R43: 10kR; R_0805_2012Metric_Pad1.20x1.40mm_HandSolder
R44: 500R; R_0805_2012Metric_Pad1.20x1.40mm_HandSolder
U17: TPS565201; SOT-23-6
U18: INA180A3; SOT-23-5_HandSoldering

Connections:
+2V: C65.1, R41.2, U18.4 (IN-), U18.5 (VS); also elsewhere on the board
+12V: C59.1, C60.1, C61.1, U17.3 (VIN), U17.5 (EN); also elsewhere on the board
/2V DVCC/BST: C58.2, U17.6 (VBST)
/2V DVCC/ISENSE_2V: C66.1, R44.1; also elsewhere on the board
GND: C59.2, C60.2, C61.2, C62.2, C63.2, C64.2, C65.2, C66.2, R43.2, U17.1 (GND), U18.2 (GND); also elsewhere on the board
unnamed: C58.1, L2.1, U17.2 (SW)
unnamed: R42.2, R43.1, U17.4 (VFB)
unnamed: C62.1, C63.1, C64.1, L2.2, R41.1, R42.1, U18.3 (IN+)
unnamed: R44.2, U18.1 (VO)

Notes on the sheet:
100 V/V
https://webench.ti.com/appinfo/webench/scripts/SDP.cgi?ID=3657E07448971878
2.1V @ 1 A
200 Hz Cutoff


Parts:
C38: 1uF; C_0805_2012Metric_Pad1.18x1.45mm_HandSolder
C39: 2.2uF; C_0805_2012Metric_Pad1.18x1.45mm_HandSolder
C40, C43, C44, C45, C46, C47, C48, C49, C50, C51, C52, C53, C54: 100n; C_0805_2012Metric_Pad1.18x1.45mm_HandSolder
C41: 1u; C_0805_2012Metric_Pad1.18x1.45mm_HandSolder
C42: 4.7u; C_0805_2012Metric_Pad1.18x1.45mm_HandSolder
C55: 10u; C_0805_2012Metric_Pad1.18x1.45mm_HandSolder
C56, C57: 2.2u; C_0805_2012Metric_Pad1.18x1.45mm_HandSolder
J8: USB_B; CUI_UJ2-BH-1-TH
J9: CAN; PinHeader_1x03_P2.54mm_Vertical
J10: Programmer; PinSocket_2x02_P1.27mm_Vertical_SMD
JP1: Jumper_3_Open; SolderJumper-3_P2.0mm_Open_TrianglePad1.0x1.5mm_NumberLabels
R39: 51kR; R_0805_2012Metric_Pad1.20x1.40mm_HandSolder
R40: 24kR; R_0805_2012Metric_Pad1.20x1.40mm_HandSolder
U14: TPS76933; SOT-23-5
U15: MCP2562; SOIC-8_3.9x4.9mm_P1.27mm
U16: STM32H750ZBTx; LQFP-144_20x20mm_P0.5mm

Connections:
+2V: C41.1, C42.1, C43.1, C44.1, C45.1, C46.1, C47.1, C48.1, C49.1, C50.1, C51.1, C52.1, C53.1, C54.1, J10.2, JP1.3 (B), U15.5 (VIO), U16.6 (VBAT), U16.17 (VDD), U16.30 (VDD), U16.33 (VDDA), U16.39 (VDD), U16.52 (VDD), U16.62 (VDD), U16.72 (VDD), U16.84 (VDD), U16.108 (VDD), U16.121 (VDD), U16.131 (VDD), U16.144 (VDD); also elsewhere on the board
+3V3: C39.1, U14.5 (OUT), U16.95 (VDD33_USB)
+5V: C55.1, U15.3 (VDD); also elsewhere on the board
+12V: C38.1, U14.1 (IN); also elsewhere on the board
/2V DVCC/ISENSE_2V: U16.27 (PC1); also elsewhere on the board
/12V Input/ISENSE_12V: U16.26 (PC0); also elsewhere on the board
/12V Input/~FLT_12V: U16.23 (PH0); also elsewhere on the board
/30V VDDA/ISENSE_30V: U16.36 (PA2); also elsewhere on the board
/30V VDDA/PGOOD_30V: U16.37 (PA3); also elsewhere on the board
/ADC + FVR/CONVST: U16.40 (PA4); also elsewhere on the board
/ADC + FVR/MISO: U16.42 (PA6); also elsewhere on the board
/ADC + FVR/MOSI: U16.43 (PA7); also elsewhere on the board
/ADC + FVR/SCK: U16.41 (PA5); also elsewhere on the board
/Amplifiers/AMP_SEL_0: U16.45 (PC5); also elsewhere on the board
/Amplifiers/AMP_SEL_1: U16.47 (PB1); also elsewhere on the board
/Amplifiers/AMP_SEL_2: U16.46 (PB0); also elsewhere on the board
/Frontend/EN_1..4: U16.44 (PC4); also elsewhere on the board
/Frontend/FAULT_1..4: U16.76 (PB15); also elsewhere on the board
/Frontend/FAULT_5..8: U16.74 (PB13); also elsewhere on the board
/Frontend/FAULT_9..12: U16.35 (PA1); also elsewhere on the board
/Frontend/FAULT_13..16: U16.28 (PC2_C); also elsewhere on the board
/Frontend/INPUT_A0: U16.22 (PF10); also elsewhere on the board
/Frontend/INPUT_A1: U16.21 (PF9); also elsewhere on the board
/Frontend/SEL_IN_2: U16.78 (PD9); also elsewhere on the board
/Frontend/SEL_IN_3: U16.79 (PD10); also elsewhere on the board
/Frontend/SF_1..4: U16.77 (PD8); also elsewhere on the board
/Frontend/SF_5..8: U16.75 (PB14); also elsewhere on the board
/Frontend/SF_9..12: U16.24 (PH1); also elsewhere on the board
/Frontend/SF_13..16: U16.34 (PA0); also elsewhere on the board
/Frontend/SINGLE_DIFF_0: U16.81 (PD12); also elsewhere on the board
/Frontend/SINGLE_DIFF_1: U16.80 (PD11); also elsewhere on the board
/MCU/CAN_RX: U15.4 (RXD), U16.135 (PB5)
/MCU/CAN_TX: U15.1 (TXD), U16.136 (PB6)
/MCU/SWCLK: J10.3, U16.109 (PA14)
/MCU/SWDIO: J10.4, U16.105 (PA13)
/MCU/USB_D+: J8.3 (D+), U16.104 (PA12)
/MCU/USB_D-: J8.2 (D-), U16.103 (PA11)
/MCU/VBUS: J8.1 (VBUS), R39.1
/MCU/VBUS_SENSE: R39.2, R40.1, U16.101 (PA9)
GND: C38.2, C39.2, C40.2, C41.2, C42.2, C43.2, C44.2, C45.2, C46.2, C47.2, C48.2, C49.2, C50.2, C51.2, C52.2, C53.2, C54.2, C55.2, C56.2, C57.2, J8.4 (GND), J8.5 (Shield), J9.3, J10.1, JP1.1 (A), R40.2, U14.2 (GND), U14.3 (~EN), U15.2 (VSS), U15.8 (STBY), U16.16 (VSS), U16.31 (VSSA), U16.38 (VSS), U16.51 (VSS), U16.61 (VSS), U16.83 (VSS), U16.94 (VSS), U16.107 (VSS), U16.120 (VSS), U16.130 (VSS); also elsewhere on the board
unnamed: C56.1, U16.71 (VCAP)
unnamed: C57.1, U16.106 (VCAP)
unnamed: J9.1, U15.7 (CANH)
unnamed: J9.2, U15.6 (CANL)
unnamed: JP1.2 (C), U16.138 (BOOT0)
unnamed: C40.1, U16.25 (NRST)

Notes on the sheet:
Internal weak pull-up
Useful documents: DS12556, RM0433, AN5020, AN5419
Added CAN in case USB ever has issues
1x 4.7u overall 100n per vdd/vbat/vdda 1u on vdda
VDD33USB supply 3V3 100mA max
Matches pins 3-6 of the STLINK-V3MINIE

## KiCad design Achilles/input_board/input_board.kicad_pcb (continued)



Board: 6 copper layers, 111.8 x 61.0 mm, 178 parts (90 on the bottom side), 169 nets.

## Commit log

2025-09-10 Updates to the RTD sensing circuit, added flash memory to the schematic.
    [Harwin_-_M80-5401042.step, PCB of Theseus.kicad_pcb, PCB of Theseus.kicad_sch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]
2025-09-20 Move theseus to subfolder
    [Harwin_-_M80-5401042.step, PCB of Theseus.kicad_pcb, PCB of Theseus.kicad_sch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]
2025-09-20 Add automedon files
    [Harwin_-_M80-5401042.step, PCB of Theseus.kicad_pcb, PCB of Theseus.kicad_sch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]
2025-09-20 Add Achilles
    [ADS8860IDGSR.stp, LM5157RTER.stp, MUX36D08IPW.stp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]
2025-09-22 Add Theseus current version?
    [PCB of Theseus.kicad_pcb, PCB of Theseus.kicad_sch, mcu.kicad_sch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]
2025-10-15 Update KiCad schematics and add power converter library
    [automedon.kicad_sch, daq.kicad_sch, ethernet.kicad_sch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]
2025-10-18 Updated schematics and symbols based on feedback
    [power.kicad_sch]
2025-10-20 Update power schematic (power.kicad_sch)
    [power.kicad_sch]
2025-10-22 Update eth subsheet
    [ethernet.kicad_sch]
2025-10-22 Update bunch of other stuff - dont touch power
    [automedon.kicad_sch, daq.kicad_sch, ethernet.kicad_sch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]
2025-10-22 updated cb1 and f1 on schematic
    [power.kicad_sch]
2025-10-22 Minor power path changes
    [power.kicad_sch]
2025-10-23 Relabel 12V
    [power.kicad_sch]
2025-10-23 Revert other files to main
    [automedon.kicad_sch, daq.kicad_sch, ethernet.kicad_sch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]
2025-10-23 Move power symbols into main sym lib
2025-10-26 Update eth ports
    [automedon.kicad_sch, daq.kicad_sch, ethernet.kicad_sch]
2025-10-31 Update connector
    [automedon.kicad_sch, ethernet.kicad_sch]
2025-11-03 Revert "Update connector"
    This reverts commit 3a37b6a19b99deb2b7118eab30d8044c58bd28a2.
    [automedon.kicad_sch, ethernet.kicad_sch]
2025-11-14 Update a bunch of shit
    [automedon.kicad_sch, daq.kicad_sch, power.kicad_sch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]
2025-11-23 Fix DAQ
    [automedon.kicad_sch]
2026-03-15 Theseus_Dev_Rev2
    It's still the same PCB
    [PCB of Theseus-B_Cu.gbr, PCB of Theseus-B_Mask.gbr, PCB of Theseus-B_Paste.gbr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]
2026-03-15 Minor routing changes
    Still the same PCB
    [PCB of Theseus-B_Cu.gbr, PCB of Theseus-B_Mask.gbr, PCB of Theseus-B_Paste.gbr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]
2026-03-15 Fixes V3
    - Copied Ferrite Bead P/N from processor
    - Added external oscillator
    - Made status LED pins pull-down
    - Copied processor programming header
    [PCB of Theseus-B_Cu.gbr, PCB of Theseus-B_Mask.gbr, PCB of Theseus-B_Paste.gbr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]
2026-03-15 NMOS and Diode Update
    Updated Diode and NMOS to support 1A max. Fixed valve state LED to draw from BATT instead of MCU.
    [PCB of Theseus.kicad_pcb, untitled.kicad_sch]
2026-03-15 Flight design, first pass
    [PCB of Theseus.kicad_pcb, PCB of Theseus.kicad_sch, bom.csv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]
2026-03-15 Flight design v1
    First pass at flight design
    [PCB of Theseus.kicad_pcb, PCB of Theseus.kicad_sch, mcu.kicad_sch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]
2026-03-15 Fix PT3 ADC
    Updated PT3 to use valid ADC pin
    [PCB of Theseus.kicad_pcb, mcu.kicad_sch]
2026-03-15 10-MAR-2026 Revisions
    [PCB of Theseus.kicad_pcb]
2026-03-15 10 MAR 2026 Changes pt 2
    [PCB of Theseus.kicad_sch, untitled.kicad_sch]
2026-03-15 change CAN transciever to 3v3, add lipo charging, change PT connectors, tidy schematic
    [PCB of Theseus.kicad_sch, untitled.kicad_sch]
2026-03-17 layout and routing + minor schematic changes
    [Harwin_-_M80-5401042.step, MicroSD_socket_Hinge_type+SDcrd.STEP, PCB of Theseus.csv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]
2026-03-17 minor fixes, generate prod files + reference files
    [PCB of Theseus-B_Cu.gbl, PCB of Theseus-B_Mask.gbs, PCB of Theseus-B_Paste.gbp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]
2026-03-19 final 3d model + pdf
    [PCB of Theseus.csv, PCB of Theseus.kicad_sch, PCB of Theseus.step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]
